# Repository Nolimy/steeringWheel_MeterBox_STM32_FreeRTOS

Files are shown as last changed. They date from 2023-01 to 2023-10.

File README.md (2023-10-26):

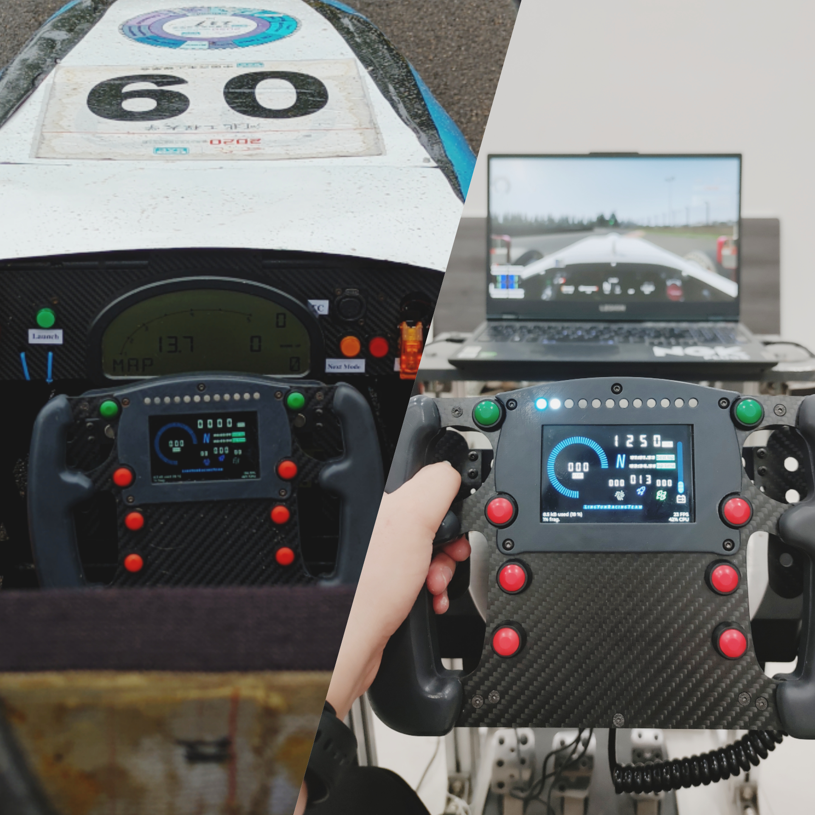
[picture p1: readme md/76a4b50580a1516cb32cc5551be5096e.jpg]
Basic Feature Set


# LY streeringWheel MeterBox

# 关于本项目

本人的本科毕业设计，一款基于STM32F407的大学生方程式赛车方向盘，具体实现功能如下：

1. 采集整车跑动数据（实车模式）以及模拟器数据（模拟器数据），并在仪表上进行实时显示。
2. 通过4G网络，对实车的跑动数据进行实时上传，实现无线数据传输功能。
3. 能够对实车的跑动数据进行采集和保存，方便技术人员对跑动数据进行复盘和分析。
4. 实现控制器功能，能够控制如神力科莎（Assetto Corsa）、神力科莎：争锋（Assetto Corsa Competizione）、F1系列等模拟类赛车游戏。
5. 为了保证实车的可用性，需要具备高亮度的屏幕保证仪表在阳光下的可视效果。
6. 具备可编程按键，实时调整车辆状态。
   
实车使用效果：



模拟器使用效果：

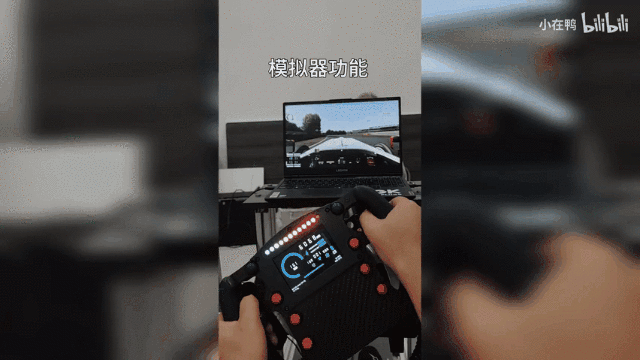
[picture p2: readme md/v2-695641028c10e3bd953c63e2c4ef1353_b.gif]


本项目适用于[大学生方程式赛事](http://www.formulastudent.com.cn/)(👈戳我了解)，因此方向盘外形是依照大学生方程式赛事规则进行设计的。

功能上，实车模式开发基于[河北工程大学凌云车队](https://lingyun.site)(👈戳我了解)凌云Ⅸ号电动方程式赛车。

模拟器功能基于[神力科莎](https://store.steampowered.com/app/244210/Assetto_Corsa/)(👈戳我了解)进行测试。

硬件工程已完整开源在[嘉立创硬件开源平台](https://oshwhub.com/nolimy/steeringWheel_project)(👈戳我了解)，您可以通过该网址访问硬件工程。

项目视频请参考[bilibili](https://www.bilibili.com/video/BV1q24y1T7iM/)(👈戳我了解)

如果项目对您有所帮助，请帮忙点亮一个免费的STAR，开源不易，感谢支持！

---

# 关于开源协议

本项目是开源项目：你可以再分发之和/或依照由自由软件基金会发布的 GNU 通用公共许可证修改之，无论是版本 3 许可证，还是（按你的决定）任何以后版都可以。

发布该项目是希望它能有用，但是并无保障;甚至连可销售和符合某个特定的目的都不保证。请参看 GNU 通用公共许可证，了解详情。

你应该随程序获得一份 GNU 通用公共许可证的复本。如果没有，请看[https://www.gnu.org/licenses/](https://www.gnu.org/licenses/&gt;%E3%80%82)



---

# 关于结构设计

方向盘的外形和结构依照大学生方程式赛事规则进行设计：

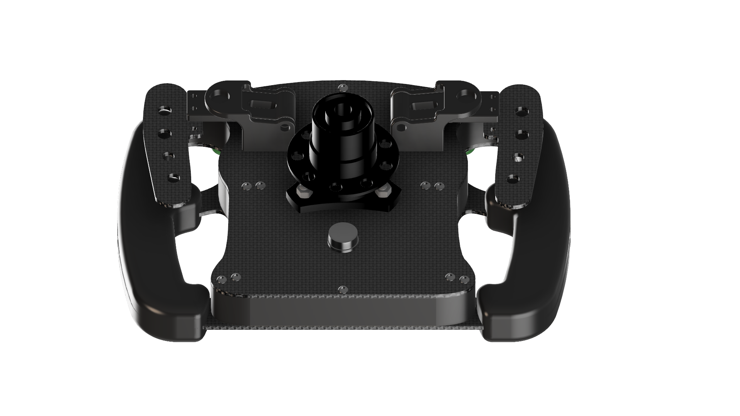
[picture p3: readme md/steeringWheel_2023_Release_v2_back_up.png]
steeringWheel_2023_Release v2_back_up.png


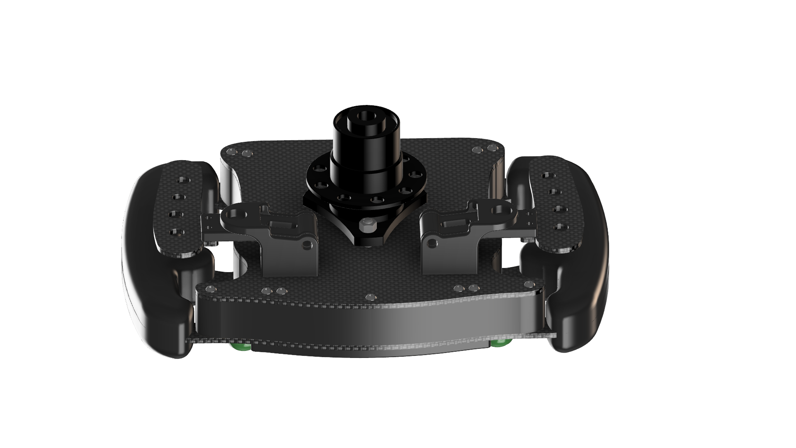
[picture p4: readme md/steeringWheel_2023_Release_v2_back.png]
steeringWheel_2023_Release v2_back.png


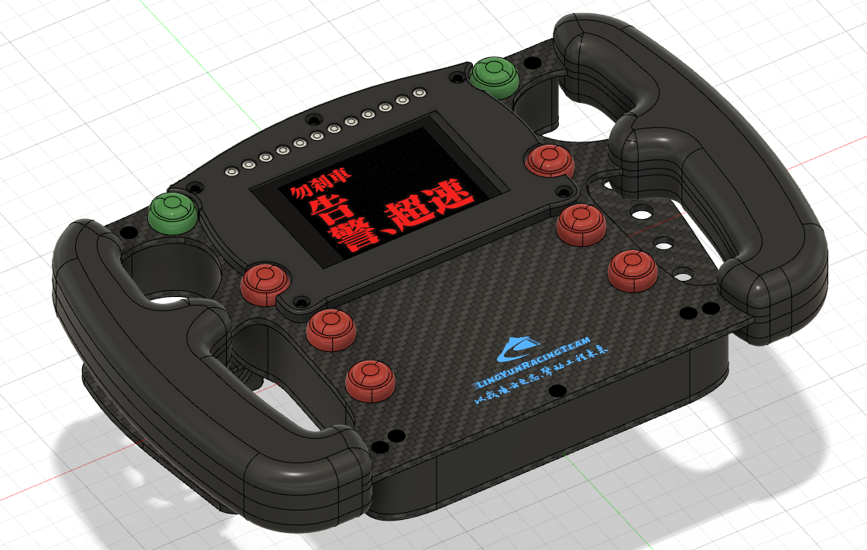
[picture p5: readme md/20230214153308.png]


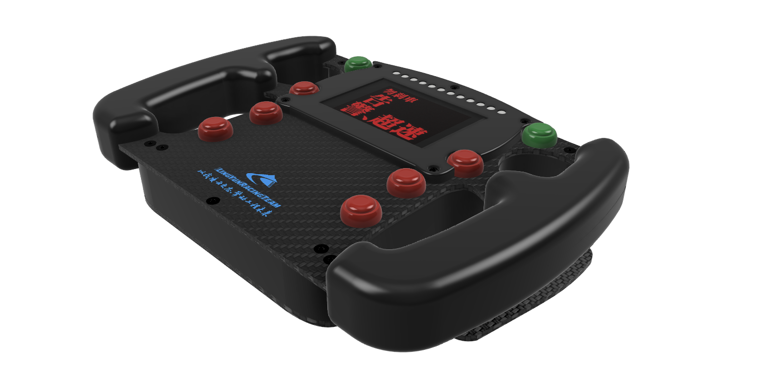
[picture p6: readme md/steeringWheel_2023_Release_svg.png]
steeringWheel_2023_Release svg.png


---

方向盘盘体宽度为250mm，高度170mm。屏幕尺寸为3.5英寸。盘体正面有8个可编程控制器按键。背面安装两个换挡拨片。方向盘上壳体和下壳体使用碳纤维板进行CNC加工，其余零部件如握把、屏幕安装罩、方向盘边缘外壳、换挡拨片连杆及换挡拨片壳体使用黑色树脂进行3D打印加工。

另外设计了一个兼容罗技G27基座的方向盘转接器，所以在我的github仓库中出现了两个3D模型，一个是使用了实车的快拆器（4滚珠），一个是使用了连接到G27的3D打印的方向盘转接器。

BOM配料单请戳👉[我](https://github.com/Nolimy/steeringWheel_MeterBox_STM32_FreeRTOS/blob/main/Steering_Wheel_BOM.xlsx)

[https://github.com/Nolimy/steeringWheel_MeterBox_STM32_FreeRTOS/blob/main/Steering_Wheel_BOM.xlsx](https://github.com/Nolimy/steeringWheel_MeterBox_STM32_FreeRTOS/blob/main/Steering_Wheel_BOM.xlsx)

完整装配模型请戳（实车）👉[我https://github.com/Nolimy/steeringWheel_MeterBox_STM32_FreeRTOS/blob/main/Model/steeringWheel_2023_Release v13.step](https://github.com/Nolimy/steeringWheel_MeterBox_STM32_FreeRTOS/blob/main/Model/steeringWheel_2023_Release%20v13.step)

模拟器：👉[我https://github.com/Nolimy/steeringWheel_MeterBox_STM32_FreeRTOS/blob/main/Model/steeringWheel_2023_Simulator_For_G27 v3.step](https://github.com/Nolimy/steeringWheel_MeterBox_STM32_FreeRTOS/blob/main/Model/steeringWheel_2023_Simulator_For_G27%20v3.step)

3D打印服务推荐嘉立创旗下三维猴：[https://www.sanweihou.com/](https://www.sanweihou.com/), 三维猴提供在线报价，CNC加工，3D打印等一站式服务。

---

# 如何使用

方向盘分为三种模式：待机模式、实车模式和模拟器模式。方向盘上电后，默认为待机模式。当方向盘收到CAN报文，则为实车模式；当方向盘收到串口报文，则为模拟器模式。在待机模式下，电脑可以识别出方向盘为USB设备，但是手柄按键无响应，此时需要使用Simhub的自定义串口设备功能给方向盘发送串口报文，方可进入模拟器模式，模拟器模式手柄按键有响应。因此，使用模拟器模式需要同时使用simhub的自定义串口设备功能。

待机模式下，SLM（换挡LED模块）12颗LED灯珠全部为蓝色。

## 大学生方程式实车使用

方向盘默认使用的是125kbps的波特率，波特率可以使用CubeMX对波特率进行配置和修改，具体CAN协议请根据自家车队的实际情况，修改BSP/CAN中的代码。

## 模拟器使用

### 方向盘连接

模拟器使用需要配合[Simhub](https://www.simhubdash.com/)进行使用。将方向盘使用USB接口连接电脑后，电脑会识别出一个虚拟串口设备和控制器设备：

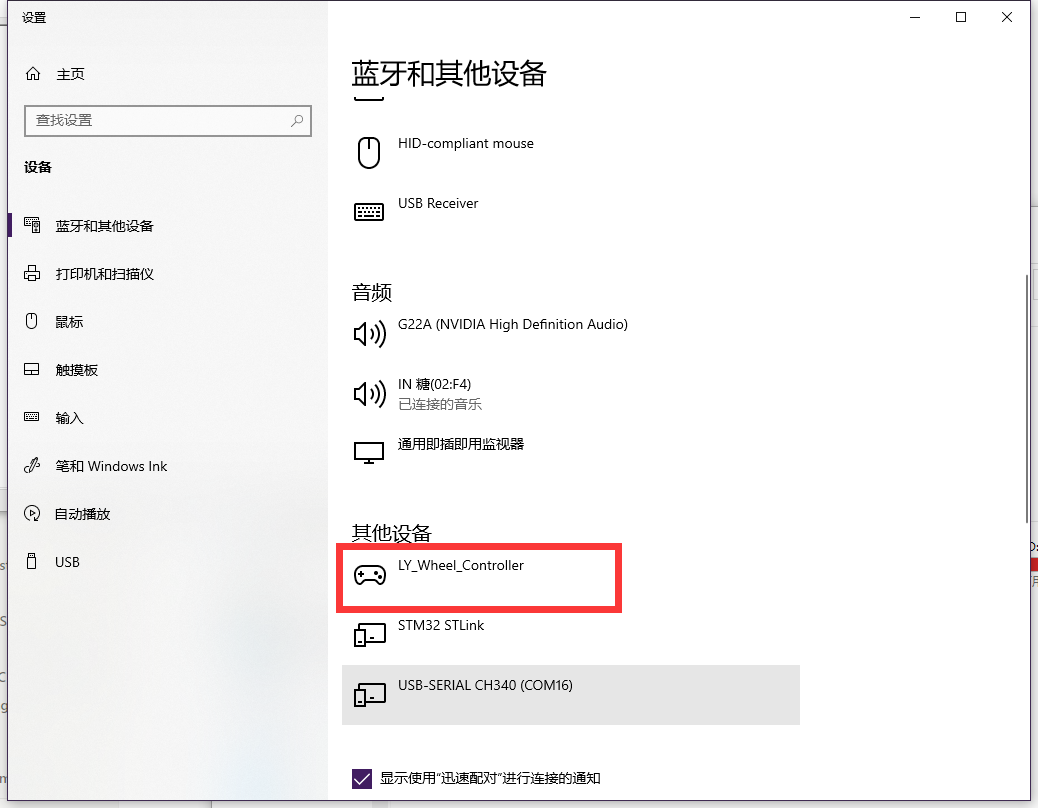
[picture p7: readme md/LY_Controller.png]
在“设置”中的“蓝牙和其他设备”中可以查看到方向盘的LY_Wheel_Controller外设。


在“设置”中的“蓝牙和其他设备”中可以查看到方向盘的LY_Wheel_Controller外设。

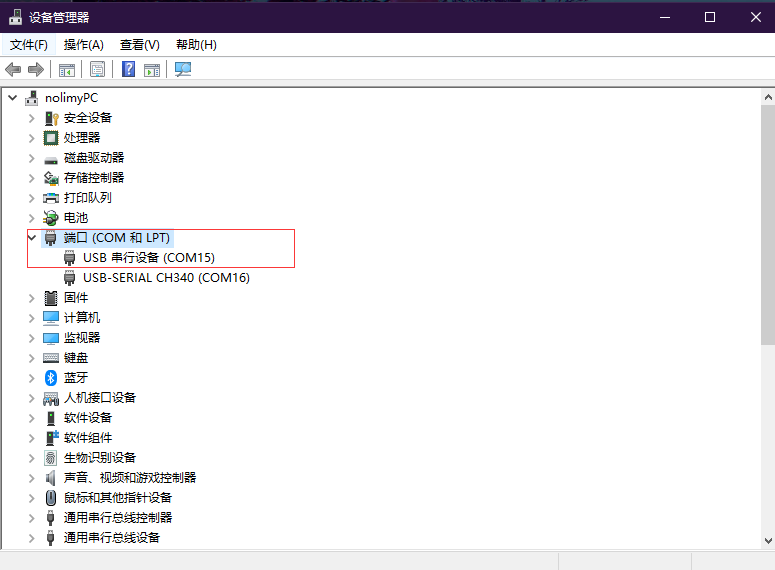
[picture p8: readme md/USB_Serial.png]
在“设备管理器”中可以查看到方向盘的虚拟串口设备及其端口号。


在“设备管理器”中可以查看到方向盘的虚拟串口设备及其端口号。

方向盘控制器的校准，点击“蓝牙和其他设备”右侧的“设备和打印机”:

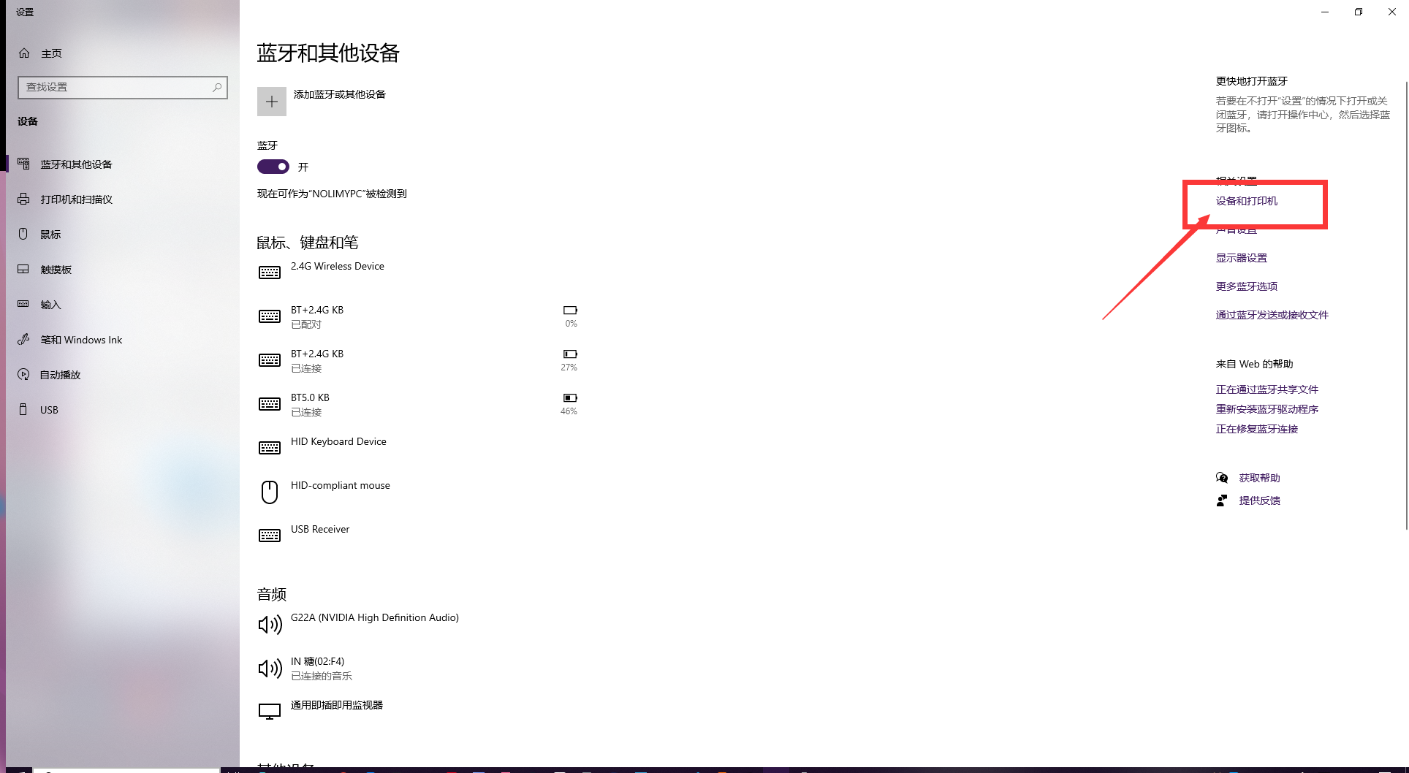
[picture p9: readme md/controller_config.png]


找到”LY_Wheel_Controller”，右键，点击 “游戏控制器设置”，然后点击“属性”.

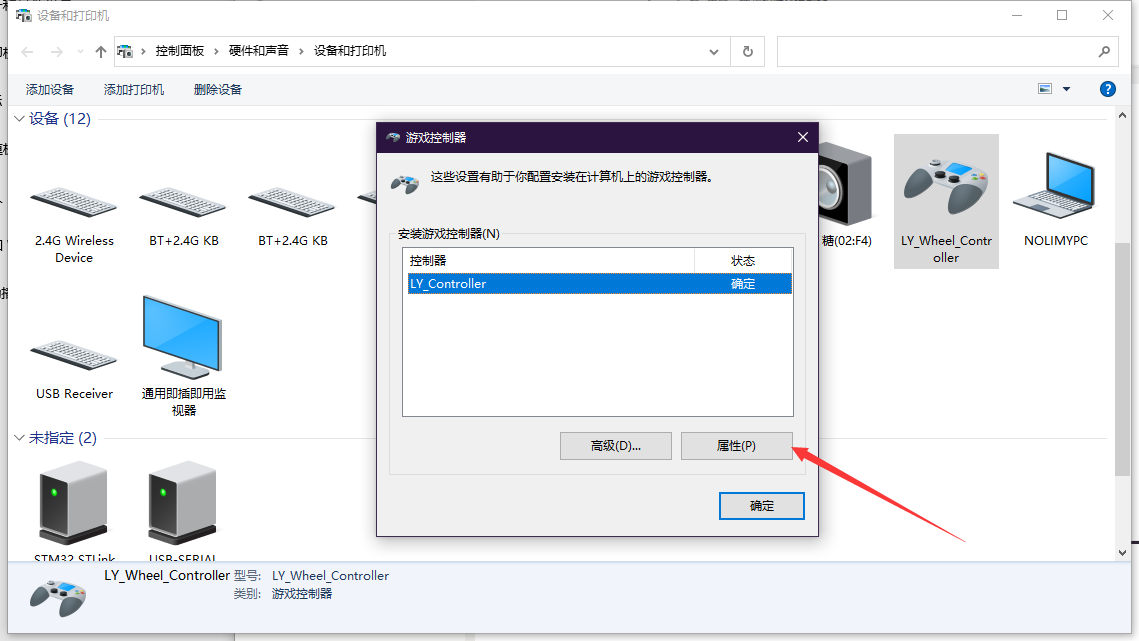
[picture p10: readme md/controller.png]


在测试页中，可以对方向盘的按键进行测试。（默认待机模式下按下方向盘按钮是没有任何反应的）

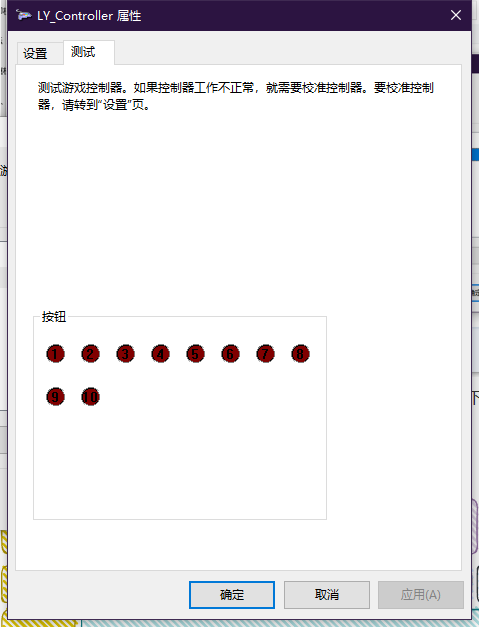
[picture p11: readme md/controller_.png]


### Simhub配置

方向盘的显示功能需要simhub配合使用，可以访问[https://www.simhubdash.com/](https://www.simhubdash.com/)下载simhub软件。这是一个非常强大的软件，支持多种模拟器游戏的数据采集，支持包括汽车仪表、arduino、G力座椅等多种外设。

安装好simhub后，打开设置界面：

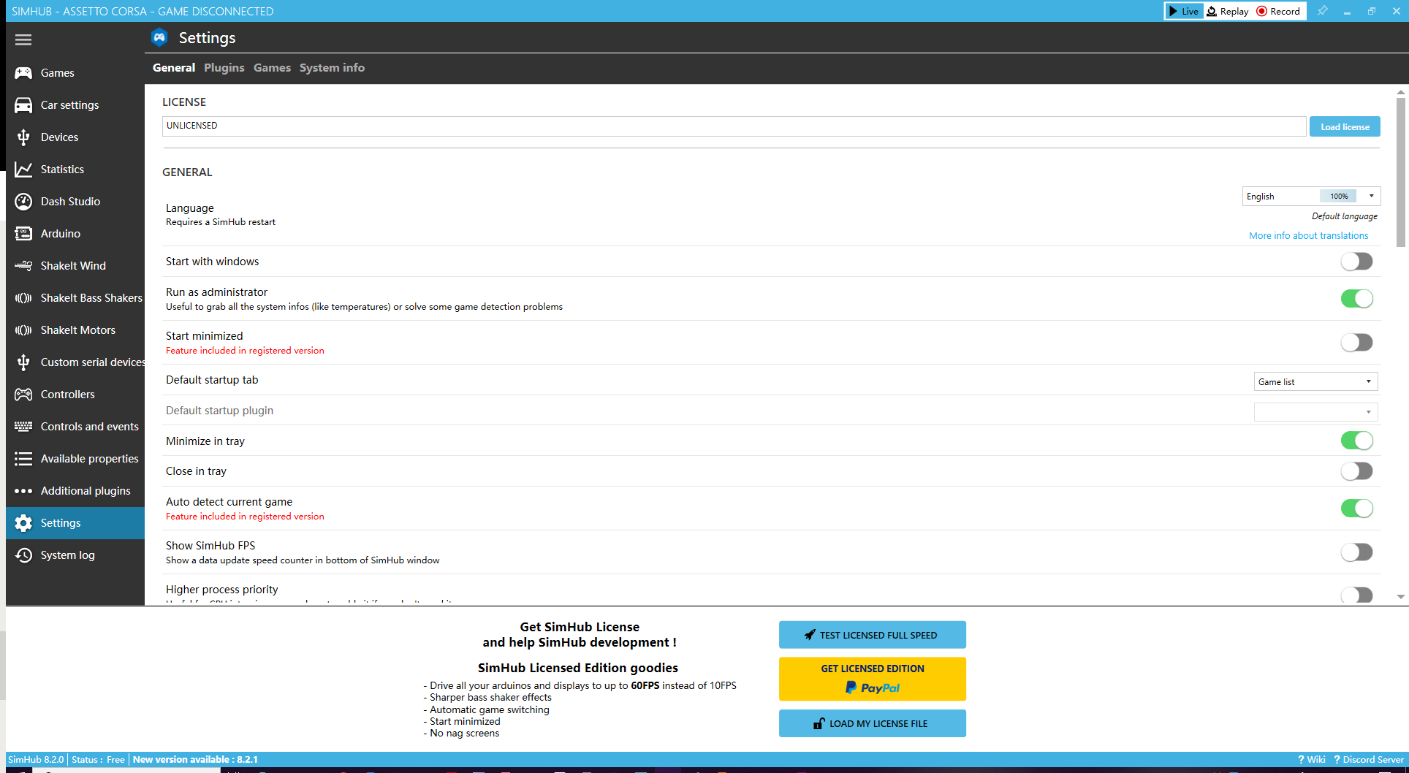
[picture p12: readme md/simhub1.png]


点击插件功能：

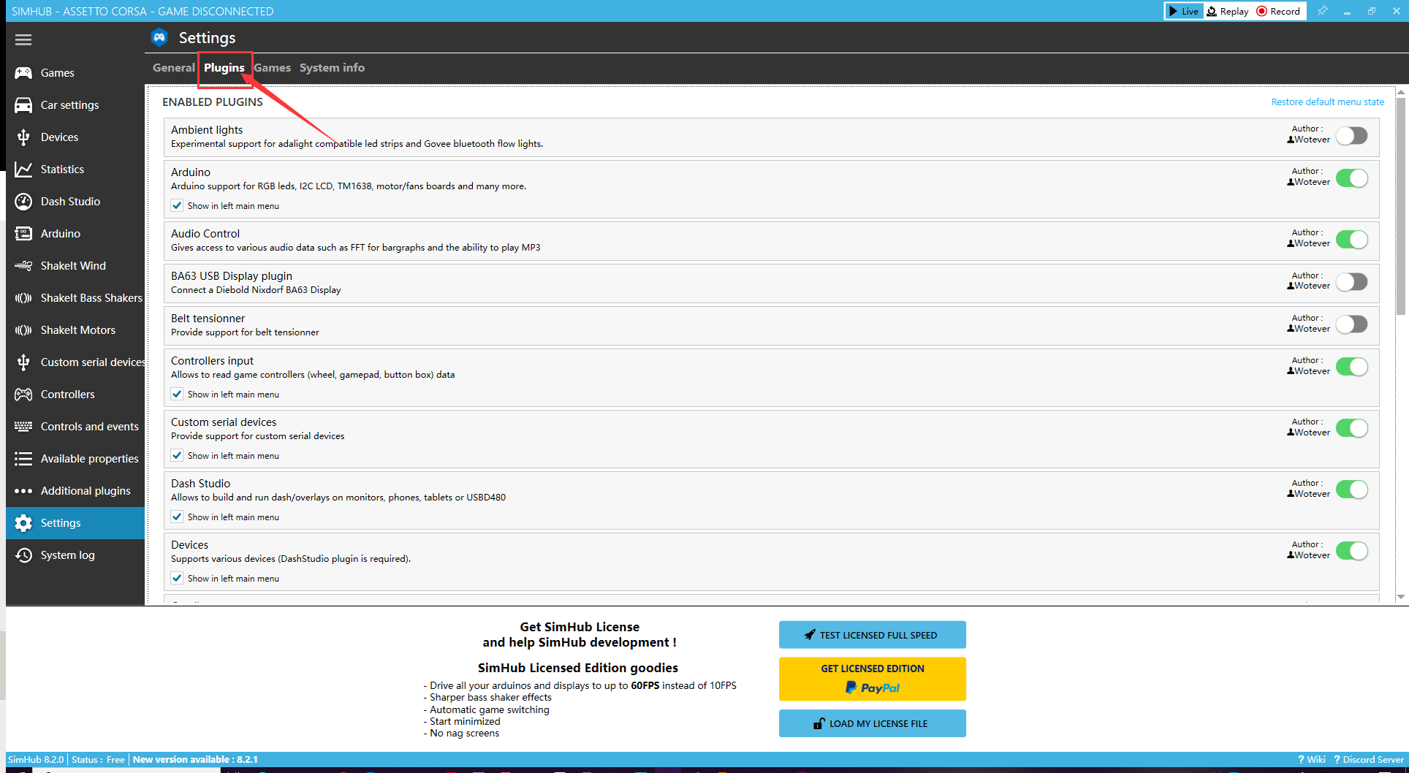
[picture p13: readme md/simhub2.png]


打开”Custom serial devices“插件：

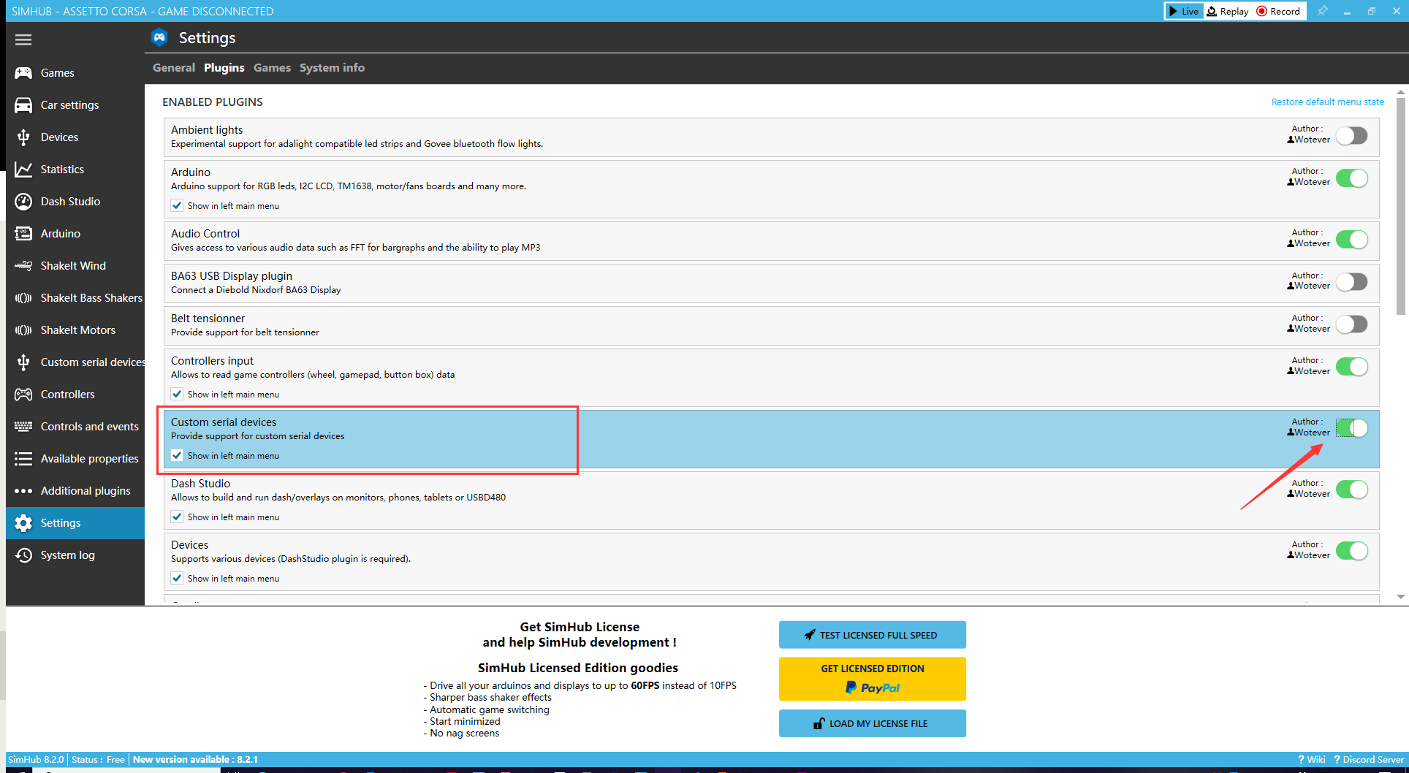
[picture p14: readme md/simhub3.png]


重新打开simhub后，左侧菜单中会出现”Custom Serial Devices”按钮：

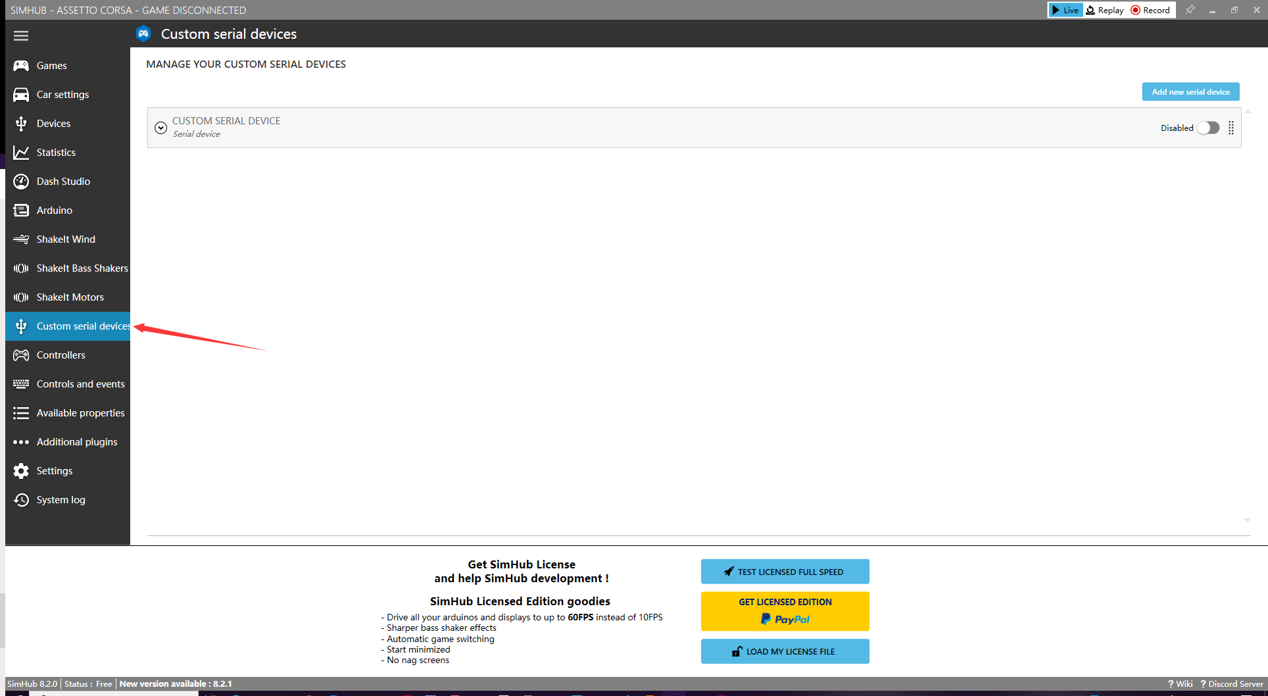
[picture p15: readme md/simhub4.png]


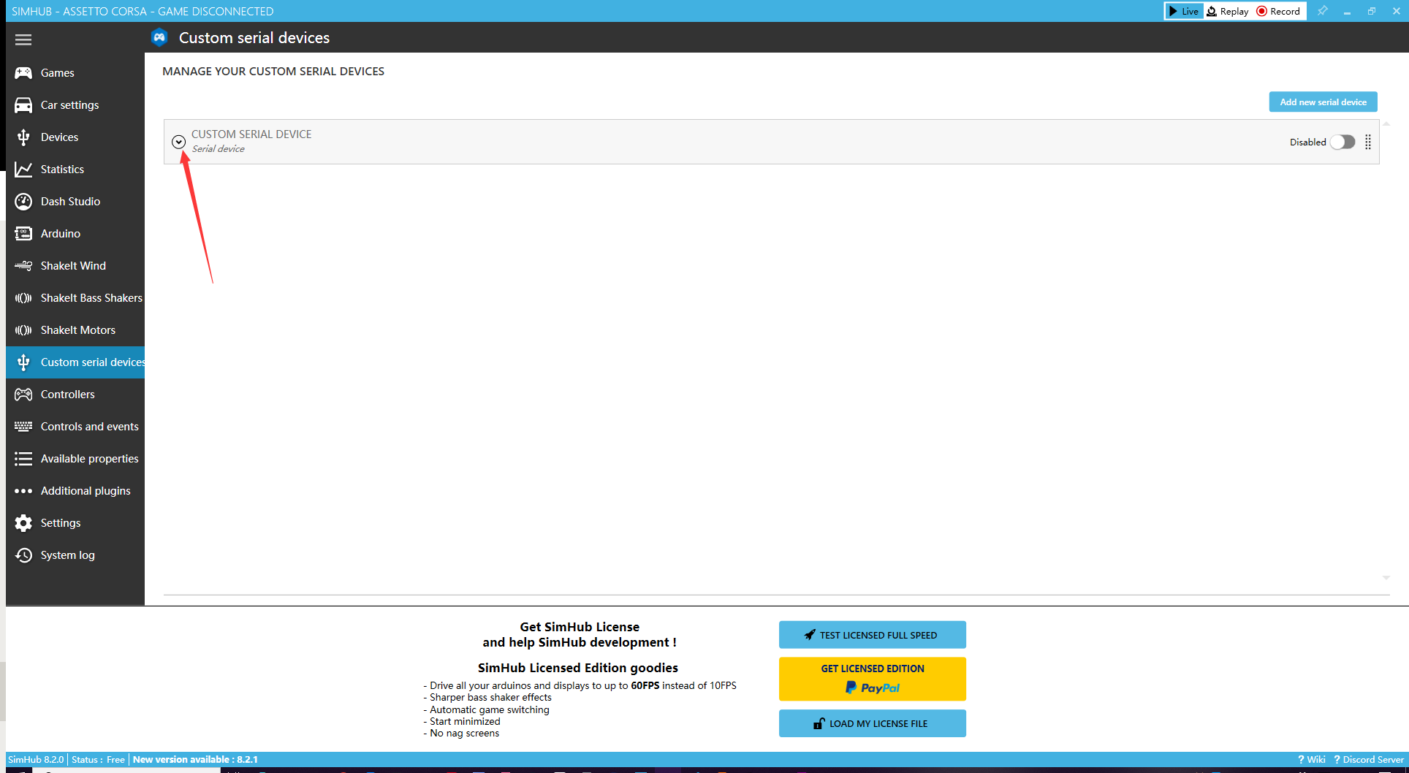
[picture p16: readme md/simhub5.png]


根据设备管理器中显示的方向盘的[串口端口](https://www.notion.so/LY-streeringWheel-MeterBox-ad02f9fb1d354ffdb82a4e431bca5e7d)，选择serial port，我这里使用的是COM15。

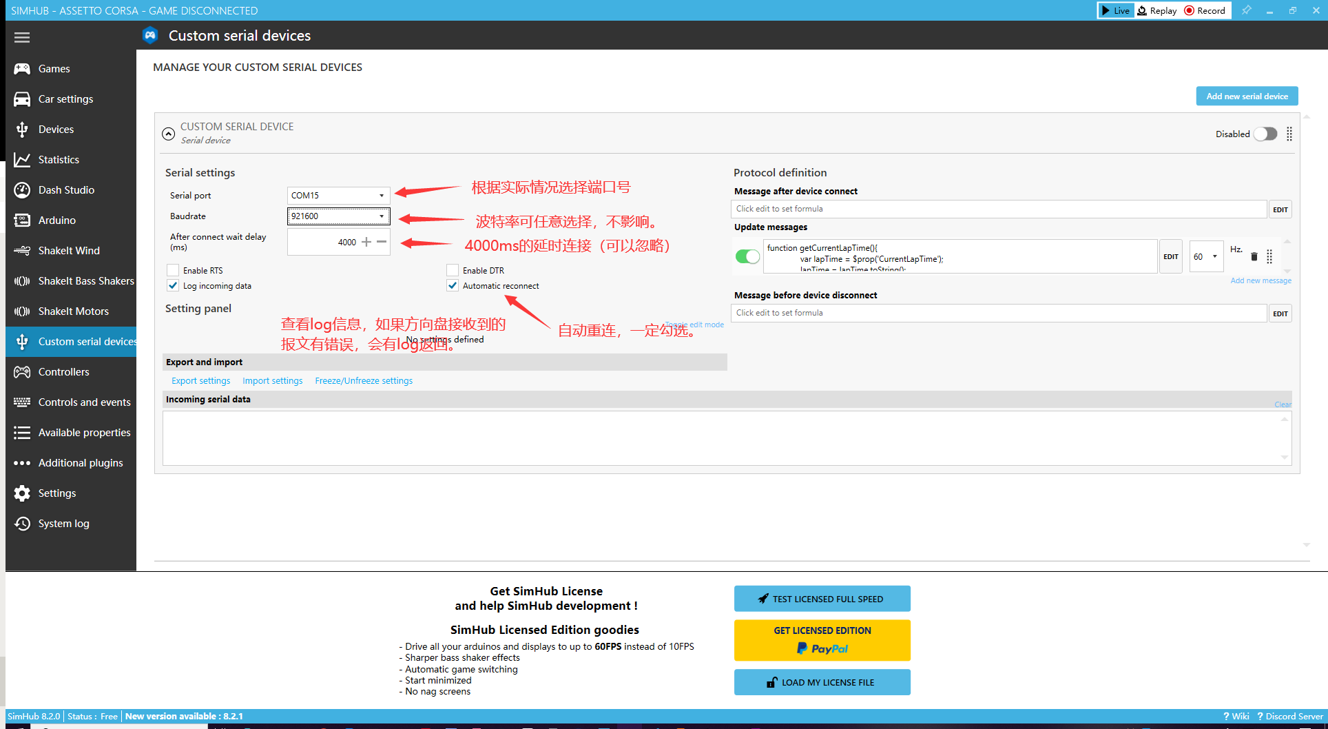
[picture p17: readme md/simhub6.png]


添加游戏数据打包json脚本，将以下javaScript代码粘贴到”Uptate messages“中：

```jsx
function getCurrentLapTime(){
	var lapTime = $prop('CurrentLapTime');
	lapTime = lapTime.toString();
	if(lapTime == "00:00:00")
	{
		return lapTime;
	}
	else
		lapTime = lapTime.toString().slice(3,11);
	return lapTime;
}
function getRPM(){
	var rpm = $prop('DataCorePlugin.GameData.NewData.Rpms');
	rpm = format(rpm,"0");
	return rpm;
}
function getSpeed(){
	var speed = $prop('SpeedKmh');
	speed = format(speed, '0');
	return speed;
}
function getGear(){
	var gear = $prop('Gear');
	return gear;
}
function getBestLapTime(){
	var bestLapTime = $prop('BestLapTime');
	bestLapTime = bestLapTime.toString();
	if(bestLapTime == "00:00:00")
	{
		return bestLapTime;
	}
	else
		bestLapTime = bestLapTime.toString().slice(3,11);
	return bestLapTime;
}
function getFuel(){
	var fuel = $prop('FuelPercent');
	fuel = format(fuel, '0');
	return fuel;
}
function getRedLine(){
	var redLine = $prop('CarSettings_CurrentGearRedLineRPM');
	return redLine;
}
function getBrake(){
	var brake = $prop('Brake');
	brake = format(brake, '0');
	return brake;
}
function getThrottle(){
	var throttle = $prop('Throttle');
	throttle = format(throttle, '0');
	return throttle;
}
function getLap()
{
	lap = $prop('CurrentLap');
	return lap;
}
var speed = getSpeed();
var carData = "{\"speed\":" + getSpeed() + ",\"rpm\":" + getRPM() + ",\"cLapTime\":" +"\"" + getCurrentLapTime() + "\"," +"\"gear\":" + "\"" +getGear() + "\"" + ",\"bLapTime\":" +"\"" + getBestLapTime() + "\""+ ",\"fuel\":"+ getFuel() + ",\"redLineRPM\":"+ getRedLine()
  + ",\"brake\":" + getBrake() + ",\"throttle\":"+ getThrottle()  + ",\"lap\":"+ getLap() +"}";
return carData;
```

点击”Edit”:

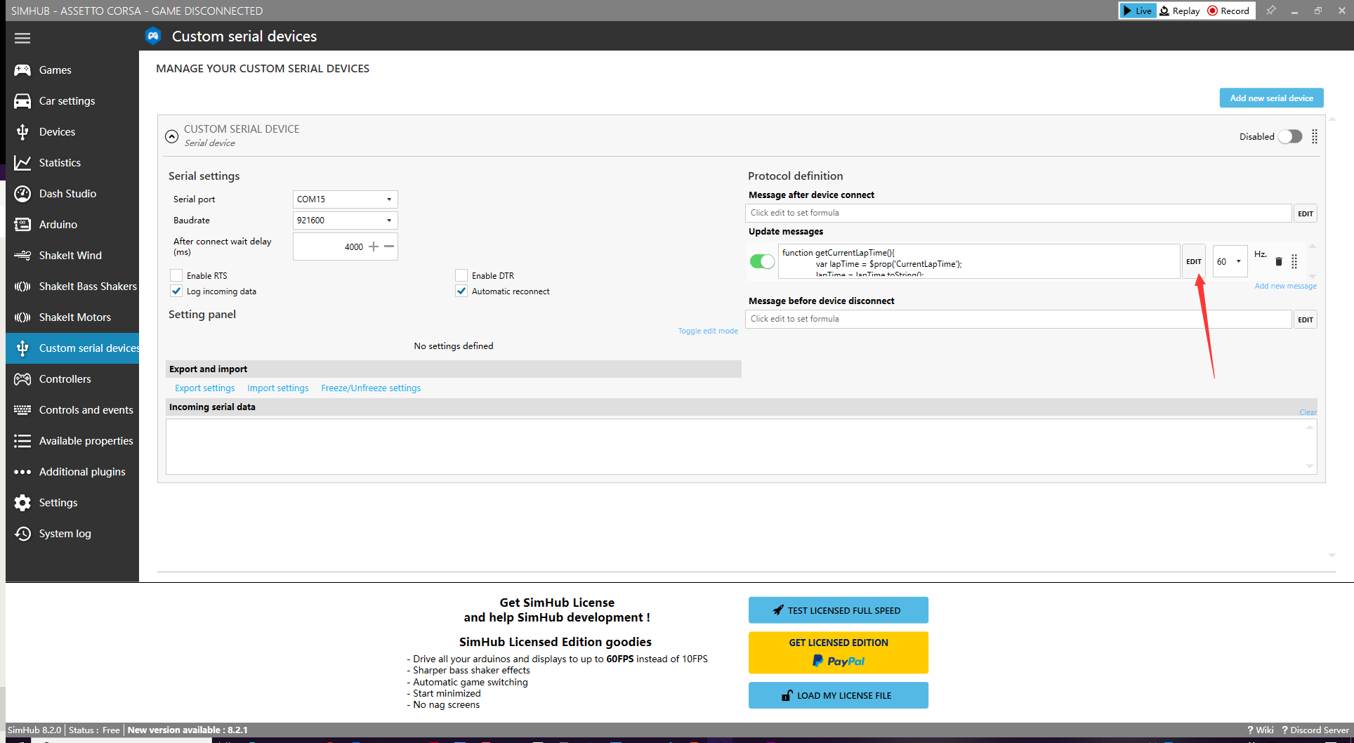
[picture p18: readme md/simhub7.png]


点击”Computed value“：

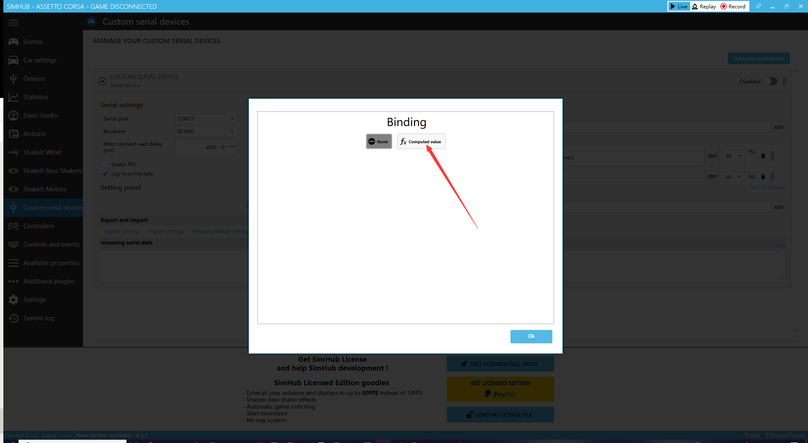
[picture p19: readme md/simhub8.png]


勾选”Use JavaScript”:

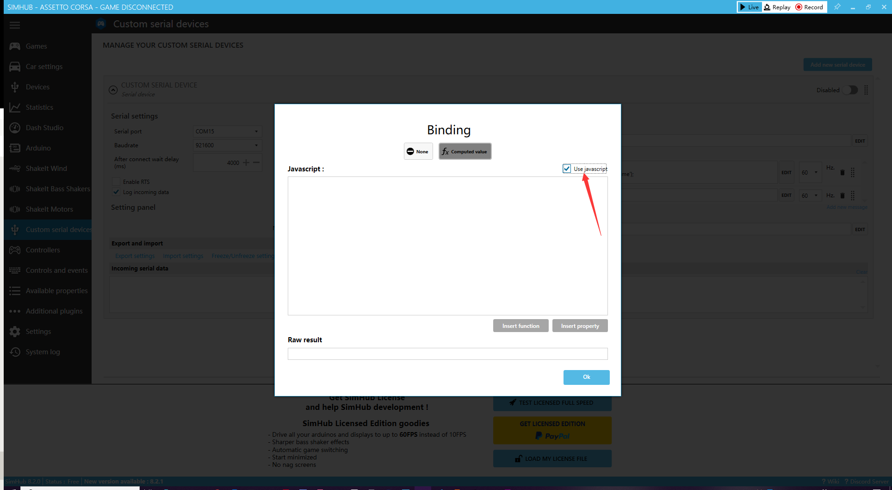
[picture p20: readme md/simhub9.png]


将[代码](https://www.notion.so/LY-streeringWheel-MeterBox-ad02f9fb1d354ffdb82a4e431bca5e7d)粘贴到文本框中：

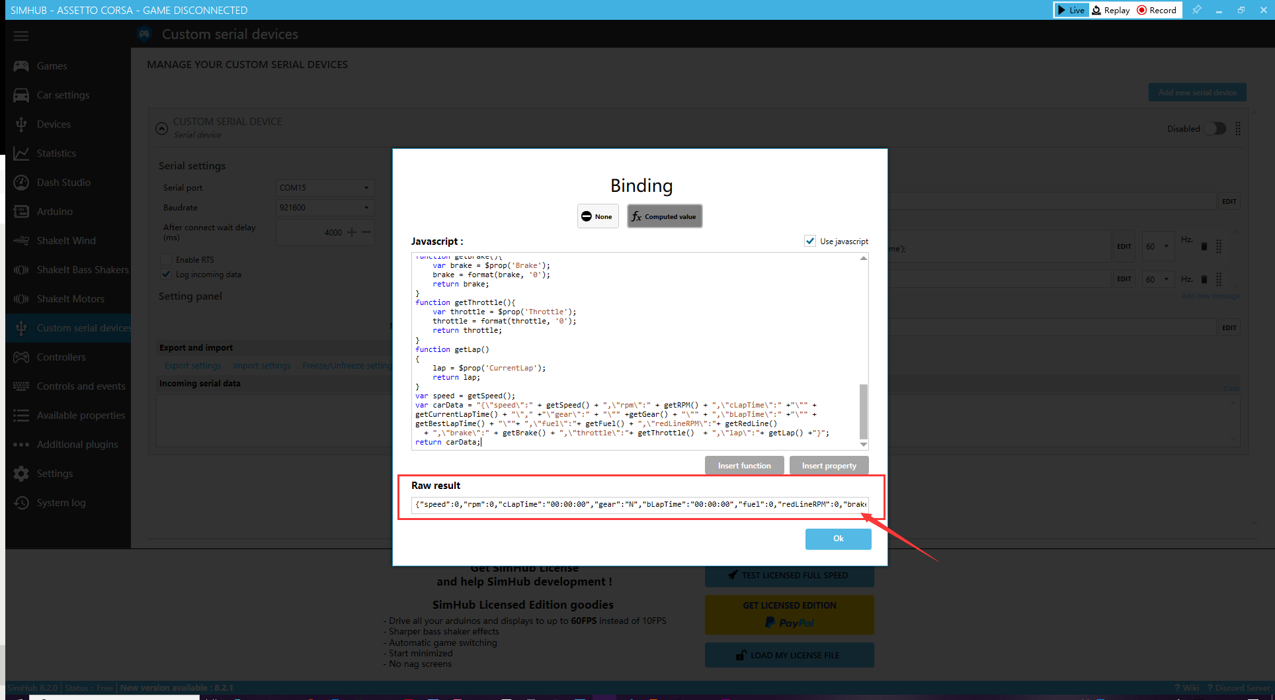
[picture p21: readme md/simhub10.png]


正常情况下Raw result中可以生成完整的json字符串。最后点击连接按钮，稍等片刻，就可以看到方向盘的SLM的全部蓝灯熄灭，此时进入模拟器模式。这时进行[手柄按键测试](https://www.notion.so/LY-streeringWheel-MeterBox-ad02f9fb1d354ffdb82a4e431bca5e7d)，可以看到按钮可以被正常检测到。



### 游戏内配置

以”Assetto Corsa“为例，在保证simhub后台运行的条件下，启动游戏。进入控制设置，将模拟器键位改成识别到的控制器按键键位，如下图：

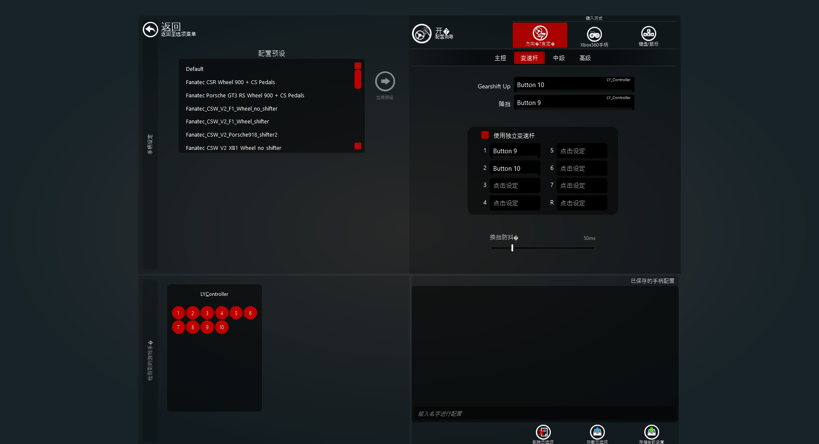
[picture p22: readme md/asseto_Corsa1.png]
asseto Corsa1.png


接下来启动游戏，就可以拥有和实车方向盘一样的体验了。

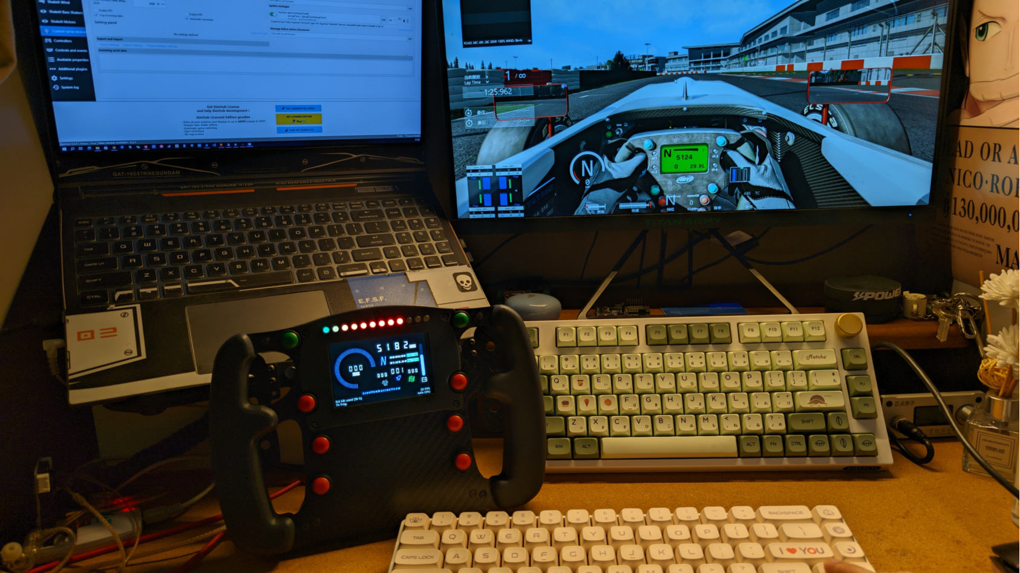
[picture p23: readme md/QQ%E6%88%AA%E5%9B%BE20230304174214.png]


# 目 录

[第1章 绪论](#绪论)

[1.1 课题研究的背景及意义](#11-课题研究的背景及意义)

[1.2 方向盘工作原理概述](#12-方向盘工作原理概述)

[1.2.1 方向盘机械结构](#121-方向盘机械结构)

[1.2.2 实车功能方案](#122-实车功能方案)

[1.2.3 模拟器功能方案](#123-模拟器功能方案)

[第2章 系统总体设计方案](#系统总体设计方案)

[2.1 硬件设计方案](#_Toc137138264)

[2.1.1 系统功能需求分析](#211-系统功能需求分析)

[2.1.2 硬件选型](#212-硬件选型)

[2.2 软件设计方案](#_Toc137138267)

[2.2.1 方向盘软件架构设计](#221-方向盘软件架构设计)

[2.2.2 MQTT服务器架构](#222-mqtt服务器架构)

[第3章 硬件开发设计及方案验证](#硬件开发设计及方案验证)

[3.1 STM32主控引脚资源分配](#31-stm32主控引脚资源分配)

[3.2 主机原理图设计](#32-主机原理图设计)

[3.2.1 STM32最小系统电路](#321-stm32最小系统电路)

[3.2.2 LCD屏幕驱动电路](#322-lcd屏幕驱动电路)

[3.2.3 BC260Y模块外围电路设计](#323-bc260y模块外围电路设计)

[3.2.4 CAN通信接口设计](#324-can通信接口设计)

[3.2.5 SLM LED电路](#325-slm-led电路)

[3.2.6 TYPE-C USB电路](#326-type-c-usb电路)

[3.2.6 其他接口电路](#326-其他接口电路)

[3.3 PCB Layout设计](#33-pcb-layout设计)

[第4章 STM32最小系统基础驱动配置](#stm32最小系统基础驱动配置)

[4.1 时钟配置](#41-时钟配置)

[4.2 STM32 SYS配置](#42-stm32-sys配置)

[4.3 数据交互层代码设计](#43-数据交互层代码设计)

[第5章 GUI仪表界面开发](#gui仪表界面开发)

[5.1 HAL层配置](#51-hal层配置)

[5.2 BSP层开发](#52-bsp层开发)

[5.3 APP层——LVGL开发](#53-app层lvgl开发)

[5.3.1 LVGL移植](#531-lvgl移植)

[5.3.2 LVGL界面设计](#532-lvgl界面设计)

[第6章 实车数据采集功能开发](#实车数据采集功能开发)

[6.1 CAN通信HAL层配置](#61-can通信hal层配置)

[6.2 CAN通信BSP层配置](#62-can通信bsp层配置)

[6.3 CAN APP层代码开发](#63-can-app层代码开发)

[第7章 模拟器相关功能实现](#模拟器相关功能实现)

[7.1 模拟器功能HAL层开发](#71-模拟器功能hal层开发)

[7.2 模拟器功能BSP层开发](#72-模拟器功能bsp层开发)

[7.3 模拟器相关功能APP层](#73-模拟器相关功能app层)

[第8章 无线数传功能开发](#无线数传功能开发)

[8.1 HAL层开发](#81-hal层开发)

[8.2 BC260Y BSP层开发](#82-bc260y-bsp层开发)

[8.3 BC260Y APP层开发](#83-bc260y-app层开发)

[8.4 无线数传测试](#84-无线数传测试)

[第9章 SLM功能模块开发](#slm功能模块开发)

[9.1 SLM HAL层开发](#91-slm-hal层开发)

[9.2 SLM BSP层驱动开发](#92-slm-bsp层驱动开发)

[9.3 SLM APP层开发](#93-slm-app层开发)

[第10章 总体功能整合](#总体功能整合)

[10.1 系统功能启动逻辑设计](#101-系统功能启动逻辑设计)

[10.2 FreeRTOS 进程配置](#102-freertos-进程配置)

[第11章 总结](#总结)

[11.1 方向盘机械结构设计](#111-方向盘机械结构设计)

[11.2 功能测试](#112-功能测试)

[11.3 待改进之处](#113-待改进之处)

[参考文献](#参考文献)

[致 谢](#致-谢)

# 绪论

## 1.1 课题研究的背景及意义

中国大学生方程式系列赛事（Formular Student China）（简称“FSC”）是一项由高等院校汽车工程或汽车相关专业在校学生组队参加的汽车设计与制造比赛。各参赛车队按照赛事规则和赛车制造标准，在一年的时间内自行设计和制造出一辆在加速、制动、操控性等方面具有优异表现的小型单人座休闲赛车，能够成功完成全部或部分赛事环节的比赛。中国大学生方程式系列赛事包括四个分赛项：中国大学生方程式汽车大赛（燃油车）、中国大学生电动方程式大赛、中国汽车工程学会巴哈大赛以及中国大学生无人驾驶方程式赛事。[1]迄今为止，我国参加FSC赛事的参赛队伍已经有超过100多支，该赛事为我国汽车工业输送了大批优秀人才，是汽车工程师的摇篮。

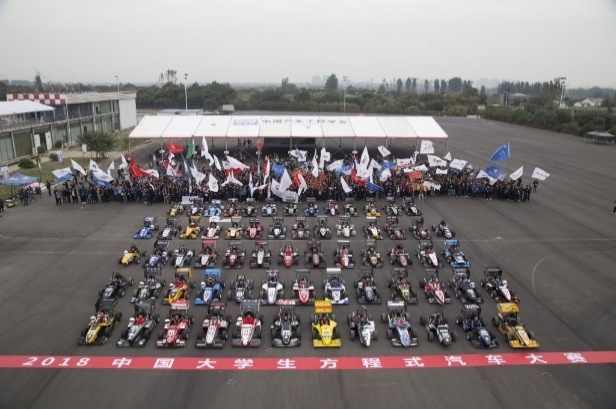
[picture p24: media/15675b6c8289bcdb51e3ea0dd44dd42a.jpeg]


中国大学生燃油方程式赛车是指使用以汽油作为动力的单座小型休闲赛车。参赛车队根据赛事规则设计并制造赛车，并进行一系列的动态跑动测试，包括直线加速、八字环绕、高速避障和耐久测试。如图1-2为河北工程大学凌云车队2020赛季参赛油车——凌云Ⅷ号赛车。该赛车搭载凯旋675发动机，使用MoTeC M800作为ECU对发动机进行自主标定和控制。该赛车使用了机械增压装置、电动离合、气动换挡、无线数传系统等设计。

中国大学生电动方程式赛车是使用电力作为动力来源的方程式赛车，如图1-3为凌云车队在2022赛季参赛的凌云Ⅸ号电动方程式赛车，该赛车使用两个EMRAX208高压轮边电机作为动力总成，使用自行设计的额定电压为444V的高压电池作为动力来源，峰值功率为150kW，最大转速为6000RPM，设计最高车速为120km/h。

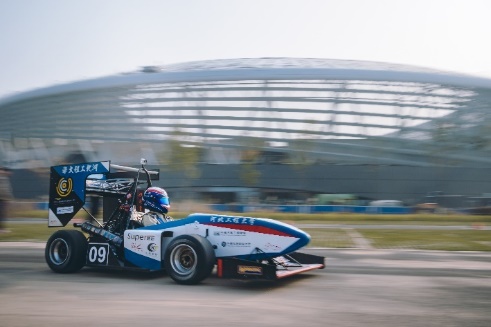
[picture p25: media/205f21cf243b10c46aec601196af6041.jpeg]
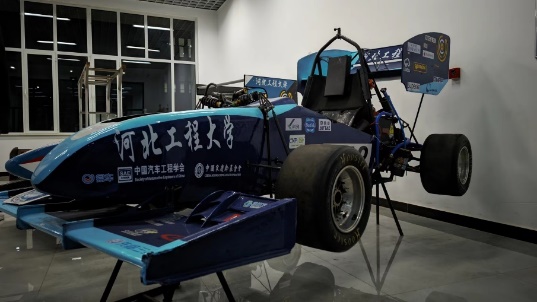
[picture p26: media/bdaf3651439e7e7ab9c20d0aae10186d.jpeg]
|  图12 凌云Ⅷ号燃油方程式赛车 |  图13 凌云Ⅸ号电动方程式赛车 |
|---|---|

在大学生方程式赛事中，各家车队使用的数据采集系统主要分为两种，一种是使用与MoTeC ECU相配套的MoTeC官方赛用仪表，如CDL3、C125等，这类仪表功能强大，具备有数据采集、数据显示、数据分析等功能，但价格普遍偏贵，市场价在2\~3万元人民币不等；另外一种是使用车队自制的仪表系统，这类仪表大都是使用普通的如LCD1602液晶显示器作为屏幕，显示效果差，但成本很低，开发难度不高。如图1-4为MoTeC的CDL3仪表，图1-5为北京理工大学使用的自制仪表屏幕面板。

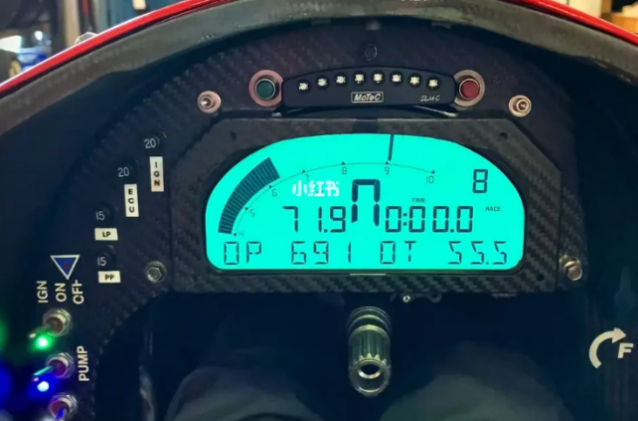
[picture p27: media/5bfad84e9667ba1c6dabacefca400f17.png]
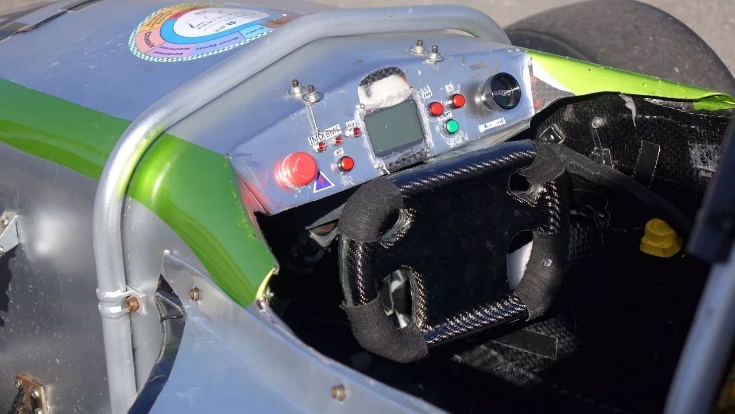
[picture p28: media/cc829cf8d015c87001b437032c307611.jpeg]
|  图14 MoTeC CDL3仪表 |  图15 北京理工大学自制仪表面板 |
|---|---|

而在更高级别的方程式赛事中，例如F1、F2方程式赛事等，这些赛车的数据采集系统是集成在方向盘上的，绝大多数赛车的方向盘作为一个独立的终端被集成在赛车中，对车辆的跑动数据进行采集，同时方向盘上的按钮可以实时控制车辆功能，例如改变当前的跑动策略，甚至与维修区的工程师进行实时通信，这就要求方向盘不但具备有基础的控制车辆转向的功能，同时可以作为一个数据采集的终端，收发车辆的数据。在为车手反馈车辆跑动状态的同时，还能够将采集到的数据实时打包发送给P房的策略师和工程师，对车辆的状态进行实时监控。如图1-6为法拉利F1车队的方向盘盘面。

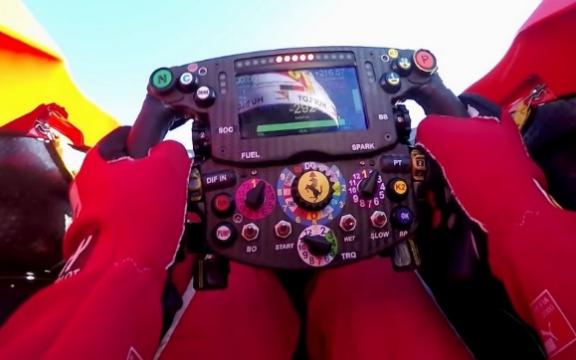
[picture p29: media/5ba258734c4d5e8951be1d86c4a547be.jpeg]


图16 法拉利F1方程式赛车方向盘

国外一些大学生方程式车队已经采用了类似上述F1方程式赛车的方向盘设计方案，将数据采集系统集成在方向盘内部，以达到更高的集成度。如下图为波兰的Wroclaw University of Technology大学生方程式赛车队PWR Racing Team的RTⅩ赛车设计并制造的使用集成数据采集系统和仪表显示的方向盘，该系统采用了自行设计的硬件系统，通过接入到赛车的整车CAN网络，对行车电脑的数据进行解算后将数据显示到屏幕。

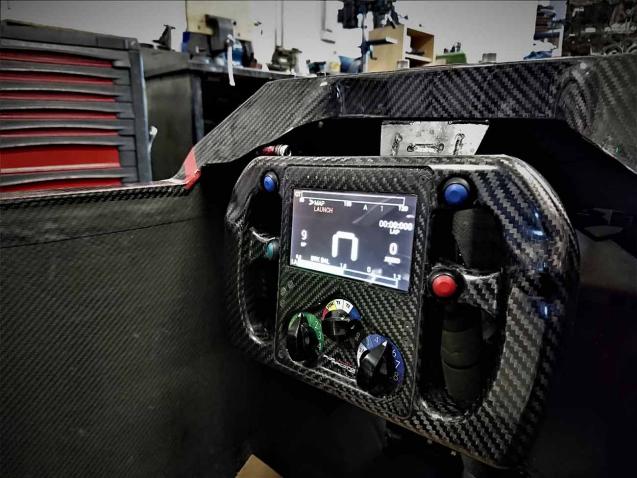
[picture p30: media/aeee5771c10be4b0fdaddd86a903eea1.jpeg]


图17 PWR RTⅩ' s Steering Wheel

动态项目作为大学生方程式系列赛事中不可或缺的比赛方式，其对车手的驾驶技能要求很高。因此，车手的日常训练就显得尤为重要。由于实车训练会导致资源消耗，如轮胎磨损、燃油消耗、场地限制等，同时具有一定危险性，因此实车训练虽然重要但是成本比较高，实际在日常练车中频率较低，车手训练更多采用的方式是使用驾驶模拟器进行训练。模拟器技术是由汽车的线控底盘技术演变而来，具备有换挡拨杆、手刹器、踏板、伺服电机转向基座等装置，基于计算机模拟技术，通过将专用的控制器接入到计算机，与相应的模拟软件配合，即可达到模拟实车驾驶跑动的目的。如下图1-8为F1方程式车手训练时使用的模拟器设备。对于大学生方程式赛事，更多车队使用的模拟器设备如图1-9所示，相较于F1等高级别方程式车手训练所使用的设备来说略显简陋，但是能达到拟真实车跑动驾驶体验的目的，对车手驾驶技能的训练有显著的提升作用。

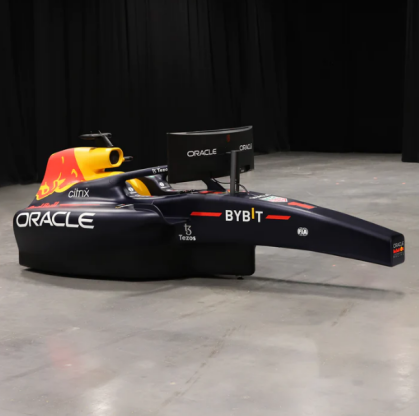
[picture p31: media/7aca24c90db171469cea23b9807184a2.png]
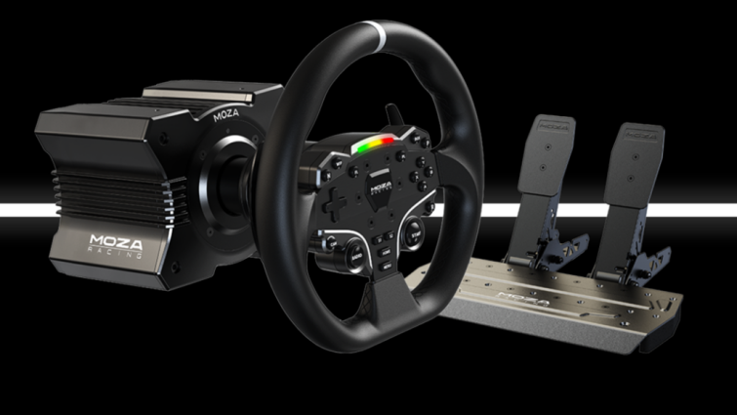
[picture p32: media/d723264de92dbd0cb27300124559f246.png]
|  图18 红牛F1车队模拟器装置 |  图19 国内市场上某品牌直驱模拟器产品 |
|---|---|

模拟器软件方面，国内大学生方程式车队中被广泛使用的模拟软件是由意大利游戏开发商Kunos Simulazioni开发的《神力科莎》（意大利语：Assetto Corsa, 英语：“Racing Setup”），如图1-10为该软件的画面。这款游戏的定义是“赛车模拟器”，通过激光扫描赛道与细致的物理引擎还原各种公路车型和赛道车型提供逼真的驾驶体验。游戏支持一系列外设，包括键鼠、游戏手柄、方向盘模拟器装置。为保证逼真的拟真体验，车手训练时会使用方向盘模拟设备使用该软件。一个很有特色的功能在于，游戏中的HUD可以通过扩展外设的方式扩展到计算机以外的其他硬件，如模拟器方向盘的屏幕上能够显示当前模拟器软件中车辆跑动的实车状态，相当于形成了一个真实的仪表。如图1-11为模拟器方向盘的仪表显示模拟器的车辆跑动数据。

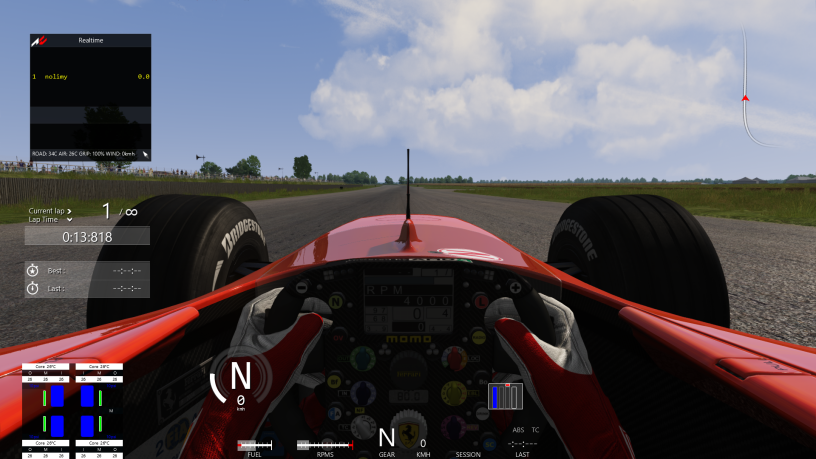
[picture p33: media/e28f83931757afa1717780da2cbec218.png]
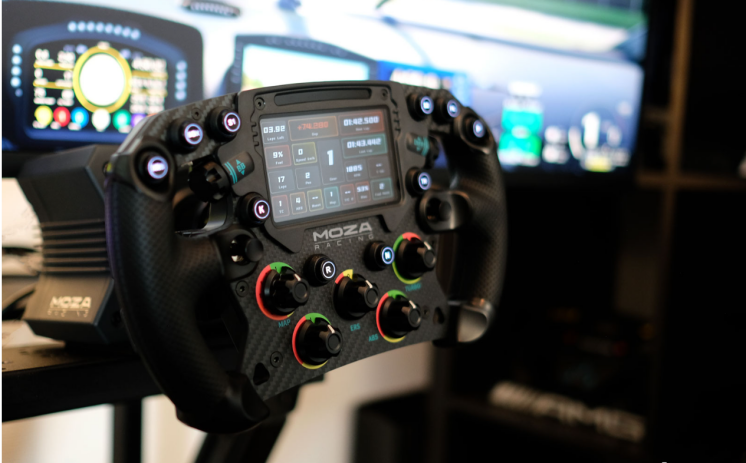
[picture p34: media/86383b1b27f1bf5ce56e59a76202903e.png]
|  图110 神力科莎模拟F1方程式赛车跑动 |  图111 方向盘显示模拟器跑动数据 |
|---|---|

综上，在大学生方程式系列赛事中，实车上使用的仪表和数据采集系统可以借鉴更高级别方程式赛车的设计思路，将其整体集成在方向盘内部，使方向盘不再仅仅是一个用于转向的工具。而模拟器上常见的带有仪表显示功能的方向盘，其外形和功能上与实车的方向盘基本一致，因此可以考虑将方向盘设计成实车和模拟器相互兼容的设备，在大学生方程式的车手日常训练时，使用同一块方向盘进行实车和模拟器的训练，对实车和模拟器的数据分别进行采集和显示。

基于上述几种当前赛场上常见的数据采集系统，本项目旨在设计一款低成本、兼容性强、功能强大、集成在方向盘中的仪表系统，具备有数据采集、仪表显示、无线数据传输等功能。同时兼容大学生方程式实车和模拟器设备。具体功能描述如下：

（1）采集大学生方程式系列赛事赛车的实车跑动数据（实车模式）以及模拟器数据（模拟器模式），并在仪表上进行实时显示。

（2）通过4G网络，对实车的跑动数据进行实时上传，实现无线数据传输功能，工程人员可以通过上位机查看赛车的实时跑动状态。

（3）实现控制器功能，能够对如神力科莎、神力科莎：争锋、F1系列模拟类赛车游戏。

（4）为保证实车在阳光下的仪表可视条件，需要具备高亮度仪表保证良好的显示效果。

（5）具备可编程按键，能够对实车功能进行控制，如进行车辆的换挡、ABS调节等功能。

（6）具备换挡提示灯条，即根据当前发动机转速提示车手进行升档降档操作的灯条。英文称之为Shift LED Module(SLM)。

## 1.2 方向盘工作原理概述

### 1.2.1 方向盘机械结构

机械结构设计主要依据《中国大学生方程式大赛规则-2022》中对转向结构及方向盘形状的规则进行设计。规则中要求：“方向盘轮廓必须为连续闭合的近圆形或近椭圆形。例如：方向盘的外轮廓可以有一些部分趋向直线，但不可以有内凹的部分。禁止使用 H 形、8 型或外轮廓有开口的方向盘。”同时规则中还要求方向盘在任何转角下的最高点都不能高于方程式赛车前环的最高点，这是对车手手部安全的保护。但由于驾驶舱内空间狭小，若是方向盘太大、太低，可能会和车手的大腿发生干涉；如果方向盘太小又可能导致车手在转向时更加费力。所以需要在多个条件限制下找到最适合的方向盘尺寸和定位设计方案。参考其他级别方程式赛车的盘面设计，采用带圆角的长方形。如下图1-12为河北工程大学凌云车队在2019赛季使用的方向盘轮廓设计。

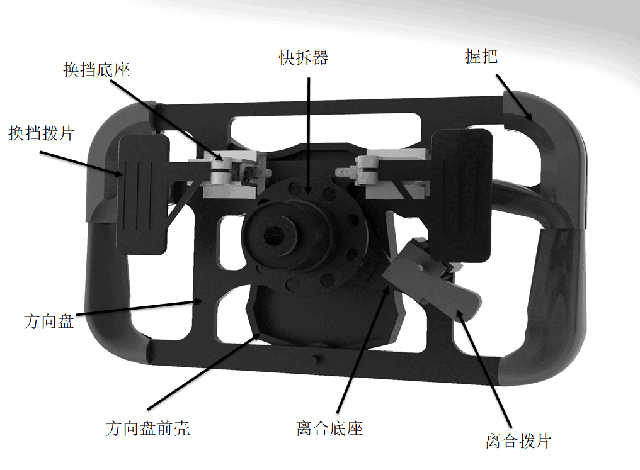
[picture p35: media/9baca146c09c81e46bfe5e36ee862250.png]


图112 凌云车队2019赛季方向盘

在制作工艺上可以选择复合材料或是3D打印来进一步轻量化。在车手握方向盘的地方可以添加手模，或是缠绕增加摩擦力的纱布，便于车手握紧方向盘。参考美国艾克朗大学ZIPS Racing方程式赛车队2019\~2020赛季的设计报告[2]，方向盘可以采用三明治结构进行设计，使用3D打印技术和CNC技术进行制造，其中，握把使用FDM 3D[3,4]打印技术进行制造，方向盘使用碳纤维板进行CNC切割。方向盘必须由坐在驾驶座上的人快速卸下，无需使用工具，因此需要通过在转向柱末端处焊接一个快速释放花键来完成，这个花键与安装在方向盘背面的一个快拆器配合使用。快拆器可以选型购买市面上常见的方程式赛车快拆器，只需在方向盘主体上依照快拆器安装螺栓位置预留好安装孔位即可。为了保证轻量化设计，方向盘主体可以进行镂空，为了保证镂空后的方向盘强度，需要对镂空后的方向盘模型进行有限元受力分析，保证方向盘轻量化设计的同时具备足够的强度。

### 1.2.2 实车功能方案

实车功能上主要分为数据采集、数据显示、车辆控制、无线数传功能四部分。其中数据采集是所有功能的基础。数据采集方面，方向盘通过CAN接口接入到整车CAN网络，通过接收并解析整车控制器或ECU在CAN网络中广播出来的特定CAN报文，即可获取到实车跑动数据，如车速、电机或发动机转速、节气门开度、踏板开度等。将采集到的CAN报文解析成物理数值后，主控芯片将相关数据渲染到仪表界面，实现数据显示功能[5.6]。车辆控制功能通过在方向盘盘面预留出按键，主控芯片通过GPIO读取按键状态，将控制信号转为CAN信号发送到CAN网络，整车控制器或者其他CAN网络中的控制单元接收相应的CAN报文进行相应功能的响应。无线数传基于4G模块，将采集的车辆跑动数据打包好通过MQTT协议发送到云端服务器实现无线数传功能。

### 1.2.3 模拟器功能方案

模拟器功能相对实车功能比较简单，通过USB将方向盘连接到电脑，方向盘作为复合USB设备，电脑将方向盘识别成两个USB设备，分别是虚拟串口和joystick控制器设备。通过Simhub软件将模拟赛车软件中的跑动数据打包成json报文从虚拟串口发送给方向盘，方向盘将解析后的跑动数据渲染到仪表界面。控制器功能基于joystick USB设备，通过编写USB的设备描述符，将方向盘的按钮开关信号采集后通过USB发送给电脑，即可实现模拟器的控制器功能。

# 系统总体设计方案

## 2.1 硬件设计方案

依据预期设计目标，该方向盘主要接收和发送CAN报文以及USB虚拟串口报文，因此需要基础的CAN收发电路和USB TypeC接口；同时使用4G模块上传数据，需要设计单独的4G模块电路；保存跑动数据到FLASH，所以需要外部FLASH的外围电路；仪表显示则需要基础的屏幕驱动电路；同时需要对实车和模拟器进行基础的控制，故需要按键电路；其他的还包括基于WS2812B LED的全彩换挡提示模块（Shift LED Module,，简称SLM），以及主控芯片基础的外围电路如晶振电路和供电电路等[7]。

如图2-1为系统总体框图。

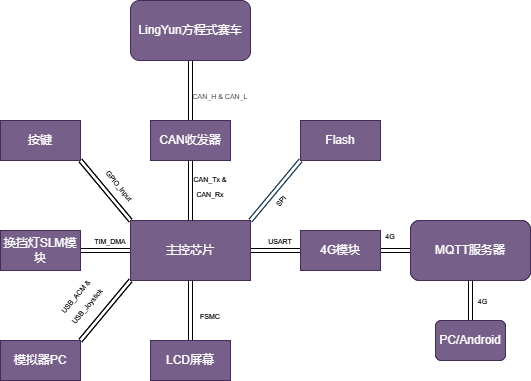
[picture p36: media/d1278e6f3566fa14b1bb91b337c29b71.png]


图21 系统总体框图

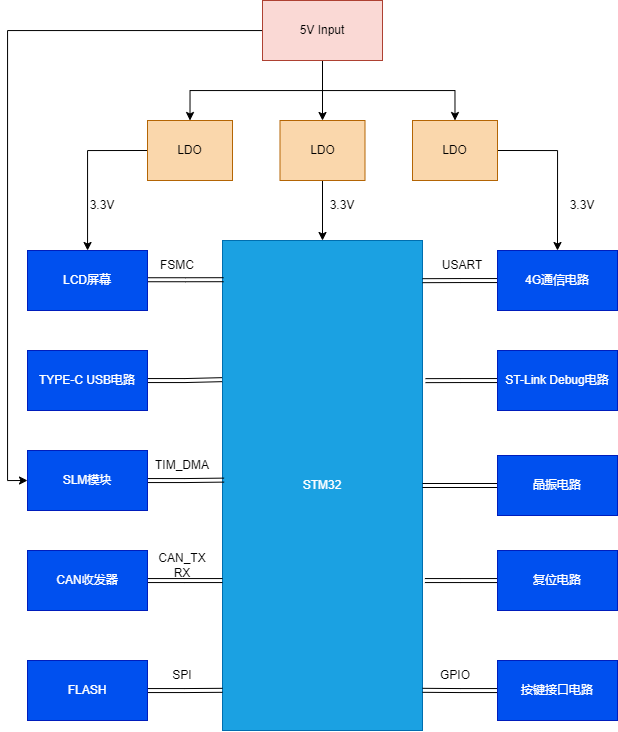
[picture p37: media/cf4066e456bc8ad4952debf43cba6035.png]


图22 硬件系统框图

### 2.1.1 系统功能需求分析

需要实现方向盘在接收到实车或者模拟器电脑发送的CAN数据或串口数据后，能够将解析好的物理数值如车速、发动机转速等渲染到屏幕上，同时在实车模式下将采集好的车辆跑动数据通过4G模块发送到云端方便其他人员查看实时跑动状态，并将数据保存到外部FLASH。方向盘具备控制功能，需要通过采集按键信号，发送相应的控制指令给车辆和模拟器。另外有独立的SLM模块能够依据当前发动机转速提示车手进行升档降档操作。

### 2.1.2 硬件选型

主控的选型，根据以上分析方向盘所涉及到的功能，我们需要主控同时具备有如下外设接口：给LCD屏幕使用的FSMC接口、与4G模块通信的至少1路的USART接口、与外部FLASH通信的SPI接口、至少1路CAN控制接口、至少3路可编程定时器、足够的GPIO接口、支持全速USB功能接口。同时为了保证仪表的显示效果，主控需要处理大量的图形界面相关的运算，因此需要至少128KB的RAM，同时为保存图片字体等图形资源，FLASH也需要足够大。主控的主频直接决定了仪表的运行效果，因此选型的主控需要有足够高的运行频率。如图2-3为本项目所使用到的所有外设接口图。

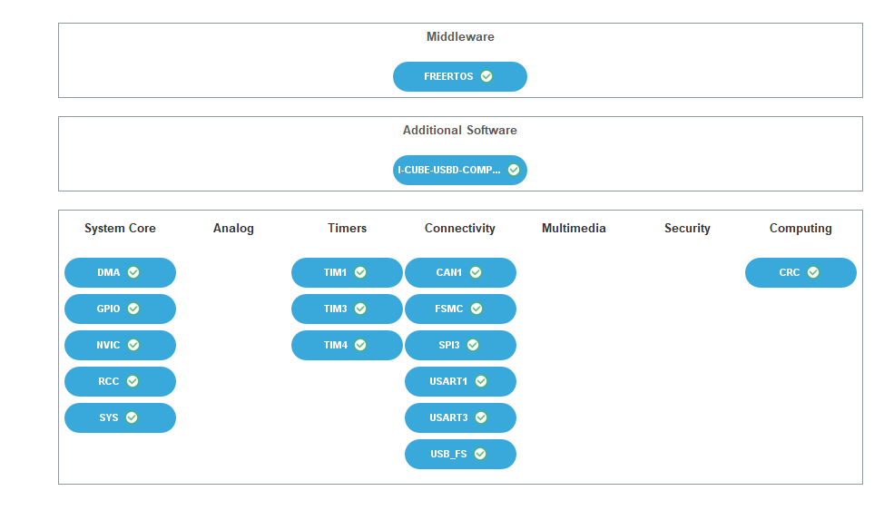
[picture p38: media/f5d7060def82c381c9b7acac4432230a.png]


图23 方向盘外设接口框图

除了主控需要具备有相应的外设资源和优异的性能以保证功能的实现，还要考虑到经济性，尽量选择价格低、货量充足的芯片作为我们的主控。最终我们选择了STM32F4系列的STM32F407ZET6，其具备有192KB RAM，512KB 片上FLASH，以及168MHz的时钟运行频率，该芯片为LQFP144封装，具备有足够本项目使用的GPIO外设接口，同时该封装便于手工焊接和贴片焊接。如图2-4为STM32F407ZET6芯片。

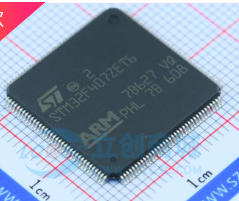
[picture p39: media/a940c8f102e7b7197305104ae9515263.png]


图24 STM32F407ZET6

4G模块上，我们选择上海移远通信的BC260Y模块，该模块支持多种网络协议：UDP/TCP/MQTT，同时具备有AT命令功能的串口，方便与主控进行通信。同时该模块能够接入到阿里云等物联网云平台，具有很强的可扩展性。

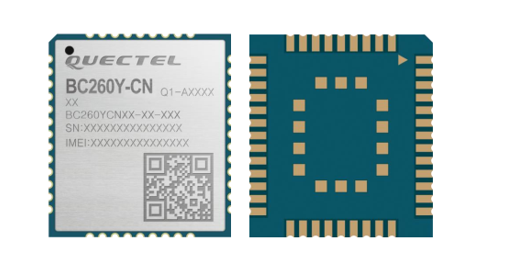
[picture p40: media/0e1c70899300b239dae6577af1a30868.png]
|  图25 BC260Y-CN |  图26 BC260Y引脚分配图 |
|---|---|

LCD屏幕选型方面，基于方向盘尺寸的考虑，我们选择使用3.5inch的屏幕。为了保证仪表在阳光直射条件下依然有良好的可视效果，市面上常见的屏幕很难满足高亮度可视需求，因此我联系到了屏幕供应商柯达科，他们提供了一款亮度可以达到1000尼特的LCD屏幕。其屏幕型号为KD035HVFMD145-01，通信协议支持SPI及8080协议。其主要参数如表2-1所示：



图27 该屏幕在阳光下的显示效果

表21 KD035HVFMD145-01

| 主控 | 材质 | 亮度 | 色彩 | 分辨率 | 尺寸 | 供电电压 |
|---|---|---|---|---|---|---|
| ST7796 | TFT  | 950cd/m2 | 65K/262K | 480\*320 | 3.5inch | 3.3V |

CAN收发器的选型上，经过综合价格、性能、供货速度等因素考量[8,9]，我采用了TJA1050芯片作为方向盘的CAN收发器。TJA1050的主要特征如下：

（1）完全符合ISO 11898标准。

（2）最高速率可达到1Mbit/s，完全符合大学生方程式赛车的CAN网络的波特率要求。

（3）电磁辐射极低，同时具备有很强的电磁抗干扰性能。

（4）保护总线引脚，防止汽车环境中的瞬态干扰。

（5）STM32的CAN控制接口为3.3V电压，赛车CAN网络为5V，TJA1050具备输入级和3.3V以及5V 的器件兼容能力。

（6）防止电池对地的短路。

SLM模块和仪表屏幕一样需要满足在阳光下可视的要求，因此选型使用WS2812B作为SLM模块的显示元件，其峰值亮度可达到1200尼特。这款LED使用PWM进行控制，仅需一个控制引脚即可实现多个LED的串联控制，具体特点如下：

（1）IC控制电路与LED点光源共用一个电源。

（2）控制电路与RGB芯片集成在一个5050封装的元器件中，构成一个完整的外控像素点。

（3）内置信号整形电路，任何一个像素点收到信号后经过波形整形后输出，保证线路波形畸变不会累加。

（4）内置上电复位和掉电复位电路。

（5）每个像素点的三基色可实现256级的亮度显示。完成16777216种颜色的全真色彩显示。

（6）端口扫描频率为2KHz/s。

（7）串行级联接口，能通过一根信号线完成数据的接收与解码。

（8）数据发送速度可达800Kbps.





图28 WS2812B典型应用电路



图29 WS2812B实物

外部FLASH选用华邦的W25Q128芯片，其具有16Mbytes的容量，可以存储大约1\~2h的实车跑动数据。该芯片使用SPI与STM32主控进行通信，同时其封装可以与华邦其他同系列的不同容量芯片相同，在保证外部电路和封装不变的情况下更换其他容量FLASH芯片十分便捷。



图210 W25Q128JVSIQ

综上所述，具体的硬件架构如下图所示：



图211 详细的硬件架构图

## 2.2 软件设计方案

软件上主要分为基于方向盘硬件的固件、无线数传所使用的MQTT服务配置以及相应的无线数传上位机开发。

### 2.2.1 方向盘软件架构设计

基于方向盘的硬件设计以及要实现的功能，我们的软件架构选择垂直结构，考虑到方向盘要实现的功能比较复杂，且实时性要求较高，因此在软件上使用到了嵌入式实时操作系统FreeRTOS，通过实时操作系统的任务进程管理，将需要同时运行的功能任务分成多个进程，分时运行。如下图2-11为系统整体架构：



图212 系统整体架构

软件层主要分为HAL（硬件抽象层）、Database（数据层）、BSP层（板级支持包）、

APP层（应用层）、操作系统。

HAL层代码通过ST意法半导体公司官方的MCU图形化配置工具生成，通过图形化界面配置好项目中使用到的外设，如串口、SPI、CAN等外设，即可生成相应的驱动代码。以串口为例，我们可以在图形界面中使能串口功能，并配置硬件控制流、中断、DMA，以及基本的波特率、字长、停止位等设置。配置完成后通过GENERATE CODE按钮即可生成相应的C代码。



图213 CubeMX串口配置页面

Database层中定义了上层应用中所使用到的所有变量和常量定义，其作用是为了避免变量的重复定义与.h头文件的重复引用和声明，使代码结构清晰，同时便于变量内存的管理，增强代码的可维护性和可读性。

BSP层是根据HAL层提供的硬件接口代码编写的，是沟通HAL层和APP层的桥梁，其作用是将APP层和HAL层分隔开，避免APP层直接调用HAL层代码，增强代码的可移植性。根据功能需求，BSP层有以下模块构成：

（1）BSP_W25Q128：对应硬件上的外部FLASH W25Q128芯片，主要调用HAL层的SPI相关代码，实现FLASH的读写操作，为APP层的FATFS提供相应的接口代码。

（2）BSP_BC260Y：对应硬件上的4G模块 BC260Y模组，主要调用HAL层的USART相关代码，实现BC260Y初始化、连接网络、错误回调等功能，为APP层的MQTT应用提供接口代码。

（3）BSP_CAN：对应硬件上的CAN收发器TJA1050，主要调用HAL层的CAN相关代码，实现CAN接收中断、CAN滤波器初始化等功能，为APP层的LY_CAN报文解析协议应用提供接口代码。

（4）BSP_USB：对应硬件上的USB接口，硬件上使用TYPEC接口连接计算机。主要调用HAL层的USB相关代码，实现USB的复合设备功能，如ACM虚拟串口接收中断、JoyStick的按键等功能，为APP层的Simhub应用提供接口代码。

（5）BSP_LCD：对应硬件上的LCD显示屏，主要调用HAL层的FSMC相关代码，基于8080协议，与LCD主控进行通信，进行基本的读写操作，提供有相应的屏幕亮屏、初始化、画点、画线等功能，为APP层的LVGL图形库提供接口代码。

（6）BSP_WS2812B：对应硬件上的WS2812B LED模块，主要调用HAL层的TIM向相关代码，基于定时器DMA输出可变的PWM波形，控制WS2812B模块的显示颜色，提供有基本的点灯函数和WS2812B的颜色控制函数，为APP层的SLM功能提供基础的接口代码。

（7）Usart_Printf：对应主控上的三路Usart，主要调用HAL层的USART相关代码，定义了printf重定向函数，方便进行项目调试，为所有APP层的模块提供printf输出接口，便于Debug。

APP层为应用代码层，定义了所有功能的具体实现的逻辑代码。为FreeRTOS系统提供接口函数。FreeRTOS的进程代码中直接调用APP层封装好的函数，如MQTT打包上传函数，SLM转速响应函数等。

FreeRTOS对APP层定义的所有功能进行统筹规划，通过FreeRTOS的进程管理，保证方向盘所有功能稳定运行。

综上所述，具体的软件架构图如下图所示：



图214 软件架构图

### 2.2.2 MQTT服务器架构

基于选用的4G模块BC260Y所支持的TCP/UDP/MQTT网络协议，综合稳定性、可维护性和成本上的考虑，选择使用MQTT（Message Queuing Telemetry Transport）协议作为无线数传的传输协议。MQTT协议是基于TCP/IP协议上为硬件性能低下的远程设备设计的基于客户端-服务器的消息发布/订阅传输协议，其特点是轻量、建议、开放，被广泛应用于物联网(IoT)设备之间的通信。其工作原理大概理解如下：

MQTT协议基于“发布-订阅”模型，其中包括两个角色，发布者（Publisher）和订阅者（Subscriber）。发布者负责发送消息，订阅者则负责接收感兴趣的消息。比如一个非常简单的使用场景：房间里有一个温度传感器，用户需要从远程获取到房间中的温度，则可以将温度传感器配置为MQTT的发布者，并定期发布当前温度的消息，而用户的手机或者电脑作为MQTT的订阅者，订阅温度消息，用户即可得到房间某时某刻的温度信息。

MQTT服务器架设在阿里云的Linux操作系统的轻量型应用服务器上，作为服务的形式不间断运行在服务器的进程中。

上位机使用QT5和C++进行编写，通过移植并调用QT官方提供的MQTT库，编写MQTT的订阅函数，完成上位机对车辆跑动数据的接收和解析显示。

# 硬件开发设计及方案验证

## 3.1 STM32主控引脚资源分配

根据功能需求，使用STM32 CubeMX图形化配置软件为STM32F407ZET6的引脚资源分配如下图所示：



图31 STM32F4芯片引脚分配

根据分配好的引脚导出的Symbol如下图所示：



图32 STM32F407ZET6 Symbol

## 3.2 主机原理图设计

使用嘉立创的国产EDA设计软件：嘉立创EDA（专业版）进行主机原理图的绘制和PCB设计。

### 3.2.1 STM32最小系统电路

STM32F407ZET6芯片的最小电路包括：供电电路、HSE晶振电路、LSE晶振电路、ST-Link下载电路、复位电路。

STM32F407ZET6使用3.3V进行供电，但方向盘整体硬件系统使用5V进行供电，因此需要一路低压差线性稳压器（Low Dropout Regulator）将5V降压为3.3V，在这里使用到了AMS1117线性稳压器，其整体电路如图3-3所示：



图33 STM32主控供电电路

根据STM32F407ZET6的数据手册的推荐HSE电路和LSE电路，我们分别选择使用8MHz的无源晶振和32.768KHz的无源晶振，并绘制原理图如下：

|  图34 HSE电路 |  图35 LSE电路  |
|---|---|

官方提供的ST-Link下载电路引脚较多，默认是使用牛角插座的封装形式，这样的封装非常占用PCB的控件，因此，我将官方提供的参考电路进行了一定简化，删除了不必要的引脚，仅保留主要的信号引脚和复位引脚，这样就节省了PCB的空间，使PCB更小。经过简化后的ST-Link下载调试电路如图3-6所示。

STM32系列芯片复位功能是将相应的GPIO引脚拉低0.5\~3ms左右的时间，即可对芯片重启。根据官方提供的复位电路参考案例，绘制复位电路如图3-7.

|  图36 简化后的下载电路 |  图37 复位电路 |
|---|---|

### 3.2.2 LCD屏幕驱动电路

屏幕驱动电路主要包括三部分：供电电路、屏幕背光电路、主控通信电路。其中，为了保证屏幕工作的稳定性，其供电的3.3V使用独立的LDO进行供电，其供电电路与图3-3相同，不再赘述。

使用的型号为KD035HVFMD145-01的屏幕主控型号为ST7796，与主控STM32的通信方式有SPI和8080两种方式。其中，SPI为三线信号传输，8080支持16线信号传输。ST7796的控制方式由IM0、IM1、IM2三个管脚决定，如下表格为ST7796的控制方式定义。

表31 ST7796控制方式

| IM2 | IM1 | IM0 | 控制方式 |
|-----|-----|-----|---|
| 0 | 0 | 0 | 18Bit 8080 |
| 0 | 0 | 1 | 9Bit 8080  |
| 0 | 1 | 0 | 16Bit 8080 |
| 0 | 1 | 1 | 8Bit 8080  |
| 1 | 0 | 1 | 3-Wire SPI |
| 1 | 1 | 1 | 4-Wire SPI |

因为使用更多的传输线进行数据传输能够增加带宽，提高屏幕的显示效果，因此我们使用16Bit的8080协议进行通信控制。使用STM32的FSMC功能，即可对8080协议进行模拟。因此与屏幕通信的电路如图所示。

这款屏幕的背光为屏幕背光为10颗LED灯珠，可以提供1000尼特的亮度，保证在户外阳光直射下的良好显示效果。其最大驱动电流为40mA，驱动电压为16V，因此需要使用Boost升压电路，将3.3V电压升压为16V。如图为根据厂家提供的设计参考改进的背光驱动电路。

|  图38 LCD控制电路 |  图39 背光驱动电路  |
|---|---|

### 3.2.3 BC260Y模块外围电路设计

BC260Y与STM32主控芯片通过串口进行通信。其主要的外围电路包括：独立的3.3V供电电路、串口电平转换电路、开机复位电路、USIM卡座电路、天线电路。其中3.3V的与上文使用相同方案，即整体电路中一共使用了三路LDO将5V转为3.3V分别给三个不同的模块供电，这里不再赘述。其他电路的设计主要参考移远通信官方提供的硬件设计参考方案，如图3-10所示。



图310 BC260Y参考电路

由于模块的串口电压域为1.8V，而STM32主控的电压域为3.3V，则需在模块和STM32主控之间增加电平转换器，这里我们选择德州仪器的 TXS0108EPWR双向电平转换器，该转换器最高数据速率为60Mbps，具有8个通道，能够满足我们的应用需求。具体电路如图3-11所示。

|  图311 电平转换电路 |  图312 德州仪器TXS0108EPWR |
|---|---|

模块的开机复位电路使用STM32主控的GPIO进行控制，官方推荐使用开集驱动电路来控制RESET引脚。模块上电后，保持RESET及BOOT（即PWRKEY引脚）输入不被拉低，即可实现模块自动开机，开机时序如图3-13所示。

依据官方提供的参考电路，MCU与模块之间的开机和复位控制电路如图3-14所示。

|  图313 BC260Y开机时序 |  图314 开机电路和复位电路 |
|---|---|

USIM卡座电路基于官方提供的参考电路进行设计，外部USIM卡通过模块内部的电源供电，不额外供电，支持1.8/3.0V供电。为了确保良好的ESD防护性能，应当加入ESD保护器件，外部USIM卡座信号走线应从USIM卡座连接到ESD保护器件后再从ESD保护器件连接到模块。完整的电路设计如图。



图315 USIM卡座电路

天线电路如下图所示：



图316 天线电路

### 3.2.4 CAN通信接口设计

STM32主控的CAN_Tx和CAN_Rx引脚与CAN收发器TJA1050的TXD和RXD引脚对应连接，并在CAN_H和CAN_L之间添加120欧姆电阻做CAN总线的阻抗匹配，以保证CAN通信的稳定性。除此之外，TJA1050应使用5V进行供电，在其VCC和GND之间增加100nF电容做滤波。



图317 CAN通信接口设计电路

### 3.2.5 SLM LED电路

SLM模块使用了WS2812B这款LED，其内部集成了处理芯片和3颗不同颜色的LED灯（红，蓝，绿），通过使用单总线协议分别控制不同颜色的亮度强弱，达到全彩显示的目的。每一个灯需要1字节的数据，故一颗WS2812B需要24Bit（3Bytes）的数据。可以采用PWM的方式进行编码，即每个PWM的周期固定为1.25us（800K），占空比为1/3时为0码，占空比为2/3时为1码。WS2812B可以将多个灯珠串联起来，通过一个总线进行控制，将多个灯珠串联后的组合视为队列，在数据传输过程中，前面的灯珠可以将前24Bit的数据留存并解析，剩余的其他数据截断后通过单总线发给线下一个灯珠。使用STM32进行控制可以使用SPI或者TIM/DMA输出PWM的方式进行控制。在本项目中我是用TIM/DMA的方式对WS2812B进行驱动，使用STM32的TIM1定时器的通道1作为信号线对WS2812B进行控制。

SLM模块的作用是根据发动机转速或者电机转速提示车手进行升档降档操作。因此，其灯珠亮灭的个数与发动机转速有关。经过基于成本以及电路驱动能力的考虑，SLM模块使用12颗WS2812B灯珠，其电路如下图所示。



图318 WS2812B电路

### 3.2.6 TYPE-C USB电路

方向盘需要通过USB线缆连接电脑，接收模拟器数据并对模拟器游戏里的车辆进行控制。USB是通用串行总线，是一种快速、灵活的总线接口，硬件上使用D+和D-两个差分信号线进行数据传输。STM32F4系列芯片支持高速USB（USB_OTG_HS）和全速USB（USB_OTG_FS），USB_OTG_HS速率最高为480M Bit/s，但此时需要外接USB HS PHY。USB_OTG_FS最高为12M Bit/s，即1.5Mbytes/s，基本满足项目需求。USB接口选择使用Type-C接口，电路设计如图3-19所示。



图319 USB电路设计

图3-19中，R12和R13两个22欧姆的电阻是高速信号线的终端电阻，其作用是为了阻抗匹配，防止信号回波反射，也有一定的抗击电流的作用。USB_FS_DP管脚处的1.5k欧姆电阻是当设备接入到主机后会被主机识别为全速USB设备。D7为一个ESD芯片，为了防止USB受到雷击或者静电损坏主芯片。

### 3.2.6 其他接口电路

方向盘接入实车和模拟器需要使用线束连接，因此需要预留出线束连接的接插件接口电路。需要预留出的接口线束定义如下表所示：

表32 线束接口定义

| 定义 | 描述 | 类型 |
|---|---|---|
| INPUT8 | 按键输入接口8 | 开关量输入 |
| INPUT7 | 按键输入接口7 | 开关量输入 |
| INPUT6 | 按键输入接口6 | 开关量输入 |
| INPUT5 | 按键输入接口5 | 开关量输入 |
| INPUT4 | 按键输入接口4 | 开关量输入 |
| INPUT3 | 按键输入接口3 | 开关量输入 |
| INPUT2 | 按键输入接口2 | 开关量输入 |
| INPUT1 | 按键输入接口1 | 开关量输入 |
| INPUT9 | 按键输入接口9 | 开关量输入 |
| INPUTA | 按键输入接口A | 开关量输入 |
| CAN_H | CAN高 | 通信接口 |
| CAN_L | CAN低 | 通信接口 |
| USB_FS_DP | USB信号线正 | 通信接口 |
| USB_FS_DM | USB信号线负 | 通信接口 |
| 5V | 5V输入 | 电源接口 |
| GND | 地 | 电源接口 |

将以上线束的接插件进行分组，INPUT1\~INPUT8接口为一组，INPUT9和INPUTA作为换挡拨片开关接口为一组，CAN_H、CAN_L、USB_FS_DP、USB_FS_DM、5V、GND为一组，选型接插件如下图3-20、图3-21、图3-22所示。

|  图320 一组按键接口16PIN接插件 |  图321 二组按键接口4PIN接插件 |  图322 6PIN接插件  |
|---|---|---|

电路原理图如下图所示。



图323 接插件电路原理图

另外预留出Debug接口，如STM32主控芯片的下载调试接口，以及串口电路，方便后期开发过程中进行调试和Debug。选型接口和电路图如下图所示。

|  图324 PZ200-2-04-W |  图325 Debug接口电路 |
|---|---|

## 3.3 PCB Layout设计

原理图设计完成进行DRC检查后将原理图转化到PCB，对PCB进行设计。由于实现功能复杂，为了简化布线布局难度，因此PCB使用四层板，从上到下依次为顶层、内层1、内层2、底层，其中顶层、底层和内层1走信号线，内层2走电源线。最终硬件Layout如下图所示。



图326 PCB Layout



图327 PCB 2D图

使用嘉立创EDA生成PCB的3D预览图如下图。



图328 PCB 3D效果图

PCB上使用到的容阻感原件全部使用0805封装，方便手工使用烙铁进行焊接。经过嘉立创打样后进行焊接，硬件实物如下图。



图329 PCBA实物

经过测试，硬件功能基本正常。

# STM32最小系统基础驱动配置

使用ST官方的STM32 CubeMX图形化代码生成工具对软件上的基础硬件驱动代码进行编写。本章节使用到的全部代码基于STM32官方HAL库。本章节主要介绍本项目中STM32主控固件的HAL层代码设计，包括STM32时钟配置、STM32 SYS模块配置以及数据交互层开发。

## 4.1 时钟配置

STM32的基础硬件配置包括RCC晶振时钟树配置、SYS配置。由于STM32芯片内部自带的时钟（HSI和LSI）在实际工程上使用会导致较大的晶振误差，导致如CAN、USB等需要进行高速通信的外设工作异常，因此我们需要将STM32的默认时钟改为使用外部晶振，来保证功能稳定。硬件上我们使用了8MHz的无源晶振，在STM32 CubeMX的时钟配置RCC菜单中选中时钟源后，将HSI改为HSE，并将晶振频率配置为168MHz，及使芯片在最高频率下运行。时钟树配置如图4-1所示。



图41 STM32 时钟树配置

## 4.2 STM32 SYS配置

为了避免ST-Link下载和Debug功能管脚占用，工程中我们应当在SYS设置中将Debug模式打开选择使用Serial Wire功能。使能Debug后，STM32芯片上的PA13和PA14管脚此时功能定义为SYS_JTMS_SWDIO和SYS_JTCK_SWCLK，防止用户占用这两个引脚用于其他功能导致下载Debug功能异常。

由于项目使用到了FreeRTOS实时操作系统，该系统会占用默认的SysTick为操作系统的始终基准源，该时钟基准源用于实现HAL_Delay()函数以及作为各种timeout的时钟基准，与默认的HAL库时钟基准源冲突，因此我们应当为HAL库选择另外一个时钟基准源。由于TIM1被WS2812B作为信号引脚被占用，因此我们选择TIM2作为HAL库的Timebase Source。修改完成后的SYS设置如下图所示。



图42 SYS设置

## 4.3 数据交互层代码设计

在整体的软件架构中，为了便于上层代码开发及内存管理，提高代码可读性，因此我将应用层使用到的变量、常量、宏定义集中进行定义和声明，在代码工程目录中创建applicationVar.c和applicationVar.h文件，.h文件主要负责对代码中使用到的变量和常量进行声明定义，上层代码开发中只需通过包含该头文件即可对定义好的变量进行调用。.c文件中负责对变量进行初始化，如对结构体进行声明等。



图43 applicationVar.h文件中对变量的声明



图44 applicationVar.c文件中对变量进行定义

# GUI仪表界面开发

## 5.1 HAL层配置

LCD屏幕主控ST7796S使用16Bit 8080协议与STM32主控进行通信。STM32可以通过其自带的FSMC资源模拟8080协议，实现LCD屏幕的驱动。FSMC（Flexible Static Memory Controller）全称为“静态存储器控制器”，支持多种存储器接口和协议，包括SRAM、NOR Flash、PSRAM等等，其中也包括模拟8080时序的LCD屏幕控制。其具有很高的灵活性，STM32的FSMC提供了多种配置选项，可以根据具体的应用需求灵活设置时序和控制信号来适配不同的外部设备接口，通过正确配置FSMC的时序参数，可以模拟8080时序接口的要求。通过使用STM32的FSMC模拟8080时序，可以减少外部逻辑器件的使用需求。传统的8080时序接口通常需要大量的逻辑门和时钟信号生成电路，而使用FSMC可以通过软件配置和控制来模拟这些时序要求。使用FSMC控制器后可以把FSMC提供的FSMC_A[25:0]作为地址线，FSMC_D[15:0]作为数据总线。STM32的FSMC硬件接口和LCD屏幕的硬件电气连接如表4-1所示。

表51 FSMC电气连接

| LCD屏幕信号线 | 描述 | STM32FSMC控制引脚 |
|---|---|---|
| D[15:0] | 数据信号 | D[15:0] |
| RDX | 读数据信号，低电平有效 | NOE |
| D/CX | 数据/命令引脚，高电平为数据引脚 | A[25:0] |
| RESX | 复位信号，低电平有效 | RESET |
| WRX | 写数据信号，低电平有效 | NWE |
| CSX | 片选信号，低电平有效 | NEX |

为模拟8080时序，我们使用STM32的A19引脚与LCD的D/CX连接，当A19拉低表示传输的信号为命令，拉高即为数据。片选信号选择使用NE2，即Bank1的第2区。

根据ST7796S芯片的数据手册得到该芯片的8080协议控制时序参数，并依据STM32F407的主频为168MHz计算后得到，读写时序中各参数应如下所示。



图51 FSMC设置

使用FSMC模拟8080时序，通过控制地址总线即可控制LCD的C/DX数据线是写命令还是数据，C/DX拉低表示为命令，拉高表示为数据。STM32F4对于16BBit位宽的地址总线会进行右移操作，比如使用地址A0时会使用Bit1，Bit0位被跳过。因此，在项目中我们使用到的A19引脚被拉低时，其写入的地址数值为0x000FFFFE(0111 1111 1111 1111 1111 0111)。根据硬件连接使用到的NE信号线，与Bank对应区域的地址进行或运算，即可写入读取信号。如下图为STM32的Bank地址对应关系。我们使用A19，NE2，故LCD屏幕寄存器的基地址为0x64000000 \| 0x000FFFFE。



图52 BANK地址

FSMC配置完成后使用CubeMX生成代码，完成HAL层功能开发。

## 5.2 BSP层开发

BSP层的主要功能是通过调用HAL层接口代码完成对LCD屏幕的读写寄存器、读写GRAM功能的开发，并基于此完成LCD屏幕的基本初始化、画点功能、颜色填充功能等功能的开发。

首先在bsp_LCD.h中对LCD的重要参数集进行定义，这里我们使用C语言中的结构体对一部分变量进行定义，如涉及到LCD屏幕宽度、高度等数据，以及坐标指令等。代码如图5-3和5-4所示。

|  图53 LCD重要参数集定义 |  图54 LCD寄存器和GRAM地址映射结构体 |
|---|---|

FSMC对8080时序进行模拟，通过写地址的形式对LCD读写时序进行模拟，根据硬件连接，对LCD对应FSMC内存基础地址进行定义，其中0x64000000为Bank1.Sector2的起始地址，0x000FFFFE是A19的偏移量。有了以上定义，LCD写命令、数据会很方便。通过宏定义LCD_WRITE_REG、LCD_WRITE_DATA、LCD_READ_DATA函数，对读写数据和命令功能进行定义。代码如图5-5所示。



图55 LCD相关宏定义

基于以上定义，对读写寄存器和数据函数进行编写，以写寄存器函数为例，LCD_WriteReg()函数具体实现如图所示。



图56 LCD写寄存器函数

通过编写好的读写寄存器等功能函数，修改厂家提供的屏幕驱动代码，编写LCD屏幕的初始化函数。该函数主要负责通过写入寄存器指令对LCD上电启动后的电源设置、颜色格式设置、GAMMA设置等初始化操作， 如图为初始化函数中的部分代码。



图57 LCD初始化代码（部分）

基于读写寄存器函数、写GRAM函数等功能函数，我们能够在屏幕上显示我们想要显示的内容，如画点、填充颜色等操作。如下图为在指定区域填充指令颜色块的函数定义。此函数也是后期我们移植LVGL的绘制接口函数，LVGL对界面图形的绘制主要基于该函数功能。



图58 LCD_Color_Fill()函数定义

至此，我们完成了LCD屏幕驱动BSP层的基本功能开发。通过在main()函数中调用LCD_Init()对LCD屏幕进行初始化，while(1)循环中使用LCD_Clear(uint16_t color)函数对屏幕进行清屏操作，即可进行屏幕显示测试。如下图为屏幕测试显示效果。



图59 屏幕纯色显示效果

## 5.3 APP层——LVGL开发

仪表界面使用开源的GUI框架LVGL进行开发。LVGL具有免费开源、轻量化、支持部件丰富、硬件接口丰富等特点，非常适合本项目使用的STM32F4主控平台。同时，其具备有丰富的资料，官方文档对各个API接口都有着详尽的描述和相应的参考案例。另外，LVGL官方提供的SquareLine Studio工具可以极大简化设计工作。项目中使用的LVGL版本为8.3.3。

### 5.3.1 LVGL移植

LVGL官方文档中有STM32平台移植LVGL的详细说明，因此主要依据官方文档对LVGL进行移植。LVGL移植的前提是已经具备有完整的屏幕显示驱动程序，前文中已经完整叙述了HAL层和BSP层对屏幕显示驱动的开发过程。

基于创建好的已经具备有完整驱动显示程序的工程对LVGL进行移植工作。首先在LVGL的官方仓库克隆完整的版本为8.3.3代码，下载的代码内容如图5-10。需要我们复制到工程中的代码主要是examples/porting下的所有文件、src文件夹、lv_conf.h、lvgl.h和demo文件（用来验证LVGL移植是否成功）。src目录下的文件为LVGL的源码，src目录中的代码如图5-11所示。Porting目录下为LVGL移植文件的模板代码，包括基本的显示驱动接口、文件系统驱动、外设接口驱动代码。移植到工程后我们需要将该目录下代码文件名中的”_template”后缀删除，如图5-12所示。Demo目录下主要是LVGL官方提供的一些测试例程，通过在LVGL的相关代码文件里使能相关宏定义即可运行官方示例代码。移植Demo目录是为了方便我们移植完毕后对移植效果进行检验，测试无误后在实际项目工程中会将相关代码删除，并关闭相关宏定义的使能。Demo目录下的代码如图5-13所示。

|  图510 LVGL完整仓库代码 |  图511 LVGL源码 |
|---|---|
|  图512 porting目录文件  |  图513 demo目录文件  |

将代码移植到STM32的工程目录中，移植后的工程目录如图所示。其中ui_design文件夹下为项目工程中实际使用到的UI设计文件和逻辑代码。



图514 移植后的LVGL代码目录

将相关代码文件添加到STM32的工程中，包括src目录下的core相关所有代码文件(core)、draw目录下的所有代码文件和其sw目录下的所有文件(draw)、extra目录下的所有文件（包括该目录下的所有子目录下的代码文件）(extra)、font目录下所有的文件(font)、hal目录下的所有.c文件(hal)、misc目录下的所有文件(misc)、widgets目录下的所有代码(widgets)，以及porting目录下的disp.c、fs.c、indev.c三个文件(porting)，最后添加LVGL的配置文件lv_conf.h和lvgl.h(config)和demo例程。添加后的代码目录如下图5-15所示。



图515 STM32 LVGL工程目录结构

将代码添加到工程中后，依据实际工程中使用的硬件进行移植修改。修改lvgl_conf.h文件中相关代码，如设置颜色格式为RGB565（依据代码注释将LV_COLOR_DEPTH修改为16），修改默认的显示刷新周期为10ms（LV_DISP_DEF_REFR_PERIOD默认为30ms）。将LV_USER_PREF_MONITOR和LV_USE_MEM_MONITOR使能设置为1来打开LVGL运行界面的FPS帧率显示和内存占用显示，方便后期调试进行仪表界面运行效率的优化。

在lv_port_disp.c和.h文件中，依据实际的硬件对显示接口代码进行编写。如图5-16所示修改屏幕的分辨率为480\*320。在lv_port_disp_init()接口函数中使用第一种定义缓存的方式即使用单缓存数组（节省RAM内存），将源代码中的Example1相关代码取消注释，并依据实际分辨率更改数组大小，如图5-17所示。修改disp_init()函数，调用BSP_LCD.c中定义的LCD_Init()代码，实现LVGL的硬件初始化代码修改，如图5-18所示。最后修改disp_flush()屏幕界面渲染更新函数，调用bsp_LCD.c中定义的LCD_Color_Fill()函数，如图5-19所示。即可完成显示接口的修改。



图516 lv_prot_disp.c分辨率设置



图517 定义显示数据缓存方式



图518 LVGL硬件初始化代码修改



图519 disp_flush()函数

完成以上修改后，LVGL的移植工作基本完成。通过在lvgl_conf.h中使能相关demo宏定义，如LV_USE_DEMO_WIDGETS宏定义使能为1，并在main函数中调用lv_init()、lv_port_disp_init()和lv_demo_widgets()函数对lvgl和Widgets Demo进行初始化，while(1)中调用lv_task_handler()，即可运行官方例程，对移植工作的效果进行验证，验证效果如图所示。



图520 LVGL例程运行效果

### 5.3.2 LVGL界面设计

仪表界面使用LVGL官方提供的SquareLine Studio软件进行设计。根据车手在驾驶时的习惯，我们需要在仪表上显示的内容包括：发动机（电机）转速、车速、挡位、圈速时间、剩余油量（剩余电量）、车辆错误码等信息。[10]其中，车手相对关注比较多的数据是车速、转速、挡位信息，因此，这些数据在界面中应当被着重显示，在UI设计中尽量突出重点。使用SquareLine绘制UI如图5-21。



图521 UI界面设计

设计的UI界面主要分为两个Screen：Startup页面和Home页面。当程序启动时，首先会显示Startup界面，该界面中的Bar进度条自行4000ms的更新动画，动画结束后进入Home页面。Home页面显示有车速、转速、挡位、圈速、发动机（电机）温度、控制器温度、油量（SOC）等信息。

通过SquareLine软件对绘制好的界面进行预览和仿真后，即可导出相应的.c和.h文件，添加到STM32工程中的LVGL/UI中进行调用，即可在STM32上进行显示。STM32平台显示效果如图5-22所示。



图522 STM32实机UI显示效果

# 实车数据采集功能开发

项目基于凌云车队2020赛季大学生方程式油车凌云Ⅷ号赛车进行实车功能开发和测试。凌云Ⅷ号赛车采用MoTeC M800 ECU，整车数据通信方式采用CAN通信，CAN波特率为1Mbps。整车CAN网络拓扑如图所示，CAN网络中CAN ID使用标准ID。



图61 凌云Ⅷ号整车CAN拓扑

## 6.1 CAN通信HAL层配置

STM32F407主控具备有两路CAN，我们使用其中一路。基于STM32 CubeMX对CAN通信进行基础配置，在软件界面中使能CAN，并依据波特率对Prescaler、Time Quanta Bit Segment 1、Time Quanta Bit Segment 2、ReSynchronization Jump Width参数进行配置。这些参数与波特率的关系式如下：

Baud Rate = APB1 peripheral clocks / (Time Quanta in Bit Segment 1 + Time Quanta in Bit Segment 2 + ReSynchronization Jump Width) / Prescaler

依据实车CAN网络波特率，我们需要将其配置为1Mbps波特率，已知STM32F407 APB1总线频率为42MHz，故取Time Quanta in Bit Segment 1为3，Time Quanta in Bit Segment 2为3，ReSynchronization Jump Width为1，Prescaler为6时，STM32的CAN1波特率为1Mbps。

其他参数配置如时间触发模式、自动唤醒模式等保持CubeMX软件的默认配置。打开CAN接收中断，使用中断方式对接收到的CAN报文进行处理。故HAL层配置结果如图6-2和6-3所示。

|  图62 CAN基本参数设置 |  图63 CAN中断配置 |
|---|---|

以上通过STM32 CubeMX生成代码，完成了CAN通信的基本HAL层配置。

## 6.2 CAN通信BSP层配置

完成HAL层开发后，基于HAL层接口在bsp_CAN.c和bsp_CAN.h中对CAN通信的BSP层进行代码开发。CAN通信的BSP层主要实现STM32的CAN过滤器设置、CAN报文发送功能开发。

首先在bsp_CAN.h中声明CAN收发报文结构体变量，其为静态结构体变量，不可被外部文件调用。声明如图6-4所示。CAN_TxHeaderTypeDef和CAN_RxHeaderTypeDef具体定义在stm32f4xx_hal_can.h中，其定义如图6-5和6-6所示。



图64 CAN收发报文结构体

|  图65 CAN_TxHeaderTypeDef定义 |  图66 CAN_RxHeaderTypeDef定义 |
|---|---|

CAN收发过滤器配置采用32位宽的掩码模式，不过滤任何CAN ID，及对接收ID的所有位都不做屏蔽，因此设置FilterMaskIdHigh 和FilterMaskIdLow都为0x0000。将通过ID的CAN报文存储到FIFO0中。CANFilter_Config()代码如图6-7所示。



图67 CANFilter_Config()函数

CAN发送报文功能需要软件配置好要发送报文的ID类型、CAN ID、传送报文的帧类型和数据长度。在整车CAN网络中，我们使用标准数据帧，方向盘仅发送数据帧，数据长度为8 Bytes。使用软件查询的方式对CAN报文进行发送。故CAN1_Send()函数如图6-8所示。



图68 CAN1_Send()函数

## 6.3 CAN APP层代码开发

CAN通信APP层主要实现整车报文数据解析、方向盘按键事件响应功能开发，基于BSP层，在CAN_app.c和CAN_app.h中对功能进行实现。

整车报文数据解析功能实现的主要思路是依据MoTeC M800 ECU发送的数据报文格式进行解析，将相关物理量如车速、发动机转速等读取到在applicationVar.h中定义的racingCarData结构体中，APP层其他平行的应用如LVGL中通过racingCarData结构体将读取到的物理量进行使用。如图为racingCarData结构体定义。



图69 racingCarData结构体定义

如图6-9中结构体油车MoTeC相关变量定义，我们主要接收的数据有机油温度、机油压力、节气门开度、氧传感器数据、ECU控制器温度、挡位、发动机温度以及基本的前轮车速和发动机转速。由于凌云Ⅷ号车未搭载前轮轮速霍尔传感器，故实际上我们无法获取到前轮轮速数据，进而无法得知准确的车速参考。为了便于测试，我们车速的实际数据来源是通过发动机转速和变速箱传动比及车辆大小链轮齿比计算得来的后轮轮速，在不考虑后轮打滑的情况下，该车速具备有一定的参考价值。

MoTeC M800一共输出4种格式各不相同的CAN报文，分别针对Dash（如CDL3等）、VCP/PDM、SLM、PLM。其中针对Dash发送的数据最为全面。根据MoTeC M800 ECU Manager我们可以得到这组CAN报文为0x5F0。M800 ECU上电以后会持续不断的在整车CAN网络发送报文，其发送频率可以在M800 ECU Manager中进行配置，默认为每秒50组CAN报文。其每组CAN报文的长度为144字节，由于CAN总线自身限制，每组报文需要分18帧进行发送，每帧报文8字节，即8 x 18 = 144字节。依据MoTeC官方的M800 CAN协议文档，我们可以得知，每组CAN报文的最后一帧的最后的第五、第六、第七字节为固定的0XFC、0XFB、0XFA，我们可以通过这三个字节判断每组CAN报文的结束帧。依据MoTeC官方提供的CAN协议文档，我们需要得到的物理量与实际CAN报文关系如表所示。

表61 M800 CAN协议

| 字节序号 | 物理量 | 单位 |
|---|---|---|
| 0:1 | 发动机转速 | 1RPM |
| 2:3 | 节气门开度 | 0.1% |
| 8:9 | 发动机温度 | 0.1℃ |
| 10:11 | 氧传感器信号 | 0.001La |
| 24:25 | 机油温度 | 0.1℃ |
| 44:45 | 低压电池电压 | 0.01V |
| 46:47 | ECU温度 | 0.1℃ |
| 104:105  | 挡位 | 1 To 1  |

依据CAN协议编写CAN解析代码，并在CAN接收中断中对解析函数进行调用，当收到CAN报文进入接收中断后，则进行CAN报文解析。如图6-10为CAN报文解析代码。



图610 CAN报文解析函数

在CAN接收中断函数中，由于MoTeC的CAN报文为多组报文，因此需要在接收完一整组共18帧CAN报文后才能对数据进行处理，如图6-11为CAN接收中断函数中处理该业务逻辑的代码。



图611 CAN接收中断接受多组CAN报文并解析逻辑代码

另外，除了兼容凌云Ⅷ号燃油方程式赛车，我们还对凌云Ⅸ号赛车的CAN协议进行了兼容。如图6-12为解析凌云Ⅸ号赛车CAN协议的代码，其原理在此不做赘述。



图612 凌云Ⅸ号赛车CAN报文解析函数

方向盘按键处理功能基于CAN通信，其工作流程为，当检测到车手按下按键后，方向盘会在整车CAN网络中发送CAN ID为0X155的CAN报文，方向盘一共有10个按键接口，对应CAN报文的10Bit数据，从按键0\~按键9对CAN报文中的Byte0\~Byte1中16个Bit的前10Bit依次置1。CAN网络中其他控制器只需通过关注相应数据位对要实现的功能进行响应即可。其具体代码实现如图6-13所示。



图613 按键处理函数

# 模拟器相关功能实现

模拟器相关功能中的模拟器数据采集基于Simhub软件实现。Simhub是一款用于模拟器赛车游戏的数据抓取工具，该软件的基础功能免费且部分开源，具有详尽的Github技术文档，支持多种竞技类游戏，如神力科莎系列、F1系列等市面上常见的模拟器游戏；同时支持多种传感器和设备，方便用户DIY模拟器游戏相关外设；支持多种输出方式，提供给用户更多选择的方式。

基于STM32的USB外设，我们将方向盘虚拟为一组复合的USB设备，分别是虚拟串口和HID游戏手柄设备，分别实现数据采集功能和游戏控制器功能。

## 7.1 模拟器功能HAL层开发

在STM32 CubeMX软件中使能USB FS功能，同时配置USB外设时钟树的相关频率为42MHz。使能完成后，CubeMX配置界面如图7-1所示。



图71 USB功能HAL配置

## 7.2 模拟器功能BSP层开发

USB复合设备开发基于Github中alambe94开源的I-CUBE-USBD-Composite配置工具。该项目作为软件包配合STM32 CubeMX进行使用，能够非常快速地配置USB复合设备。通过Clone项目到本地，并在CubeMX软件中安装、使能该软件包，即可进行使用。如图7-2为USB Composite功能配置界面，使能了CDC_ACM设备和HID_MOUSE设备，在代码生成后，通过基于MOUSE修改其设备描述符，将HID_MOUSE设备更改为HID_JOYSTICK设备实现游戏控制器功能。



图72 USB Composite配置界面

完成配置后生成代码。此时编译工程并将代码烧录到STM32，使用USB将方向盘PCBA接入到计算机后，会被识别为一路USB串口设备和一路鼠标设备。

在生成的usbd_cdc_acm_if.c代码中，修改CDC_Receive()函数，该函数为虚拟串口接收中断函数。当虚拟串口接收到串口数据后会进入该中断进行数据处理。由于STM32的虚拟串口的缓冲区大小有限仅为256Bytes，故当串口数据超过256字节时会造成数据的丢包。因此我们需要在程序上进行循环队列缓冲，在接收数据时先将数据放入到缓存区，直到接收到字符串的结束符完成一组串口数据的接收。修改后的CDC_Receive()函数如图7-3所示。



图73 CDC串口接收中断函数

修改HID_MOUSE相关代码文件中的设备描述符部分，首先修改配置描述符，将原来代码中声明的MOUSE设备修改为NONE设备，代码如图7-4所示。



图74 配置描述符修改

修改USB设备的设备描述符如图7-5所示。



图75 JOYSTICK设备描述符代码

最后修改usbd_desc.c中对复合设备的描述相关代码如下图。



图76 USB复合设备定义

修改完成后编译工程，将代码烧录到硬件并通过USB线缆连接到计算机，方向盘即可被识别为虚拟串口设备和JOYSTICK设备，如图7-7和7-8所示。

|  图77 USB虚拟串口设备 |  图78 USB控制器设备 |
|---|---|

游戏手柄的按键读取功能定义在Bsp_USB_Composite.c中。其按键读取功能代码如图7-9所示。



图79 USB按键读取功能函数

此时使用windows控制面板中的游戏控制器校准窗口，即可对方向盘上的按键功能进行测试。如图所示。

|  图710 设备管理器手柄设置 |  图711 设备管理器手柄按键校准测试 |
|---|---|

## 7.3 模拟器相关功能APP层

APP层主要实现模拟器数据接收功能的数据栈协议。Simhub采集模拟器游戏数据后将数据通过JavaScript脚本打包为json字符串，通过虚拟串口将打包好的json报文发送给方向盘，方向盘根据json报文进行解析即可获取模拟器游戏内车辆跑动的物理量。Simhub打包json脚本的JavaScript代码如图7-12所示。其接收到的数据以结构体形式保存，类似CAN通信功能中定义的racingCarData结构体，在applicationVar.c中我们也定义了一个sh_CarData的结构体。



图712 Simhub打包json字符串脚本及打包好的字符串

其打包好的json字符串形式为：

{"speed":0,"rpm":4000,"cLapTime":"00:55.92","gear":"N","bLapTime":"00:00:00","fuel":53,"redLineRPM":17900,"brake":0,"throttle":0,"lap":1}

STM32的APP层通过移植的开源json库cJson的相关代码，即可对接收到的json字符串进行解析。



图713 JSON报文解析函数

# 无线数传功能开发

## 8.1 HAL层开发

无线数传基于移远通信的BC260Y-CN模块[11]，是一款低能耗高性能的NB-IoT模块。通过3GPP Rel-13和3GPP Rel-14无线电通信协议与网络运营商的基础设备建立通信。该模块在方向盘硬件中通过串口与STM32主控进行通信，其默认的串口通信波特率为9600bps，为了保证满足单位时间内上传报文的数据吞吐量，在项目中我们需要提高其与STM32主控之间的通信波特率到460800bps。因此，HAL层开发主要配置STM32与BC260Y相连接的USART3串口，并开启串口的相关中断。HAL层配置如图8-1和8-2所示。

|  图81 串口波特率配置 |  图82 打开串口中断 |
|---|---|

生成代码后，在生成的串口HAL相关代码中添加printf()函数重定向代码，将printf()重定向到串口，方便后期调试工作进行串口调试。本项目中一共使用了两路串口USART1和USART3，USART3与BC260Y连接进行通信，USART1用于与电脑通信进行调试输出。因此，printf()函数中定义了两路串口打印输出，用户可通过usartTxFlag变量控制printf()函数输出的是哪一路串口，当usartTxFlag = 1时则使用串口1进行打印输出，usartTxFlag 为其他值时使用串口3进行打印输出。其代码如图8-3所示。



图83 串口重定向函数

## 8.2 BC260Y BSP层开发

BC260Y的BSP层主要进行对APP层发送AT指令的字符串和接收到的BC260Y的串口回显数据进行处理，其中包括cmdToBC260Y函数、BC260Y_init函数和串口接收中断函数。

cmdToBC260Y函数为发送AT指令给BC260Y并判断是否有效的函数。其定义为：

uint8_t cmdToBC26Y(char \*strSource, char \*strTarget, uint8_t okCheck);

其中，strSource为AT命令字符串。strTarget为若AT指令BC260Y成功响应后发送回的字符串。okCheck为是否进行模块回调字符串包含”OK”字符，因为一些AT命令发送给模块后回显命令仅”OK”两个字符，这类情况需要单独进行处理。若BC260Y回显字符串中包含成功响应后需要检查的strTarget，则返回1，否则返回0。该操作会重复五次，若超过五次均为响应成功则判断超时，直接return 0处理。该函数的具体代码如图8-4所示。



图84 cmdToBC260Y函数

BC260Y_init()函数为BC260Y模块初始化函数。其通过在上电后拉低模块的RST引脚进行短暂复位操作后对模块进行开机操作。BC260Y开机后会自动尝试联网操作，若联网成功，会通过串口返回当前的IPV4地址，字符串形如：“IP: 192.168.10.226”。如果联网不成功，未返回带有“IP”字符的字符串，则初始化操作失败，此时应当检查BC260Y的硬件是否错误，如天线连接是否异常或SIM卡是否未插。IP连接成功后会进行SIM卡检查、关闭休眠模式、查询信号质量等操作，这些信息会通过串口1打印到调试人员的电脑上。初始化代码如图8-5所示。



图85 BC260Y初始化函数

串口接收函数主要业务逻辑是将BC260Y的回显命令字符串进行初步处理。因为BC260Y的回显字符串格式上较为难以处理，因此需要将其中的部分不必要的字符如”\\r”等进行删除操作。同时在接收中断中会有如MQTT服务器连接是否成功等回显字符串的判断，若判断成功将相应的标志位进行置1。为了避免数据溢出，会在代码中加入memset函数对缓存数组中的数据处理完毕后进行清空。代码如图所示。



图86 串口接收中断

## 8.3 BC260Y APP层开发

STM32主控对BC260Y基于其官方定义的AT指令进行通信。如下表格列举了在本项目中使用到的AT指令及其描述。

表81 AT指令表

| AT指令 | 用途 | 返回值 |
|---|---|---|
| AT\\r\\n | 测试指令 | OK or Error |
| AT+CIMI\\r\\n | 查询有卡无卡 | 460xxxxxxxxx or ERROR |
| AT+CSQ\\r\\n | 查询信号质量 | +CSQ:22,0 or +CSQ:99, 99 |
| AT+CGATT?\\r\\n | 查询网络连接 | +CGATT:1 or +CGATT:0 |
| AT+QSCLK?\\r\\n | 配置休眠模式 | OK |
| AT+IPR = 460800\\r\\n | 配置波特率为460800 | OK |
| ATE0\\r\\n | 关闭命令回显 | |
| AT+QMTOPEN=0,”MQTT.Server”,1883\\r\\n | 打开MQTT服务器 | OK +QMTOPEN:0,0 |
| AT+QMTCONN=0,”BC260Y”,”User”,”passwd”\\r\\n | 连接MQTT服务 | OK +QMTCONN: 0,0,0 |
| AT+QMTPUB=0,0,0,1,"hello",11,"hello world"\\r\\n | 发布消息 | OK |

STM32主控启动BC260Y的流程如图所示。APP层主要依据BC260Y的BSP层接口进行开发，其代码主要在MQTT_App.c和MQTT_App.h中。在BC260Y初始化成功后，会进行MQTT服务的打开并连接服务器。项目中使用到的MQTT服务器基于阿里云的轻量应用型服务器进行搭建，基于开源的MQTT消息代理Eclipse Mosquitto，其实现了基于MQTT 3.1协议版本和3.1.1版本的轻量、适用于低功耗NB-IoT设备的完整服务器软件架构。通过在服务器部署并配置Mosquitto Server，放行云服务器的MQTT相应1883端口，即可完成对服务器的搭建。



图87 BC260Y运行流程

MQTT_App.c中主要定义了以下功能函数：mqttServiceStartup()、MQTT_Init()、jsonPack()和MQTT_Pubdata(char \*json)。其中，mqttServiceStartup()函数使能串口中断，并调用BSP层的BC260Y_init()函数和APP层的MQTT_Init()函数，并依据BC260Y_init()函数的返回值和MQTT_Init()函数的返回值操作PCBA上预留的两个LED进行亮灭，方便调试人员在不连接串口的情况下了解网络和MQTT连接状况，若二者都初始化成功，则PCB上的两颗LED全部亮起。MQTT_Init()函数和mqttServiceStartup()函数分别如图8-8和8-9所示。



图88 MQTT_Init()函数



图89 mqttServiceStartup()函数

MQTT_Pubdata(char \*json)函数是将打包好的json字符串经过与BC260Y的发布消息AT命令“AT+QMTPUB”字符串进行组合后通过串口发送给BC260Y模块。其代码实现如图所示。



图810 MQTT_Pubdata(char \*json)函数

jsonPack()函数是将实车跑动数据进行json打包函数，通过sprintf()函数，将从实车CAN网络中解析得来的车速、转速等信息打包到json0[]数组中。打包好后，通过MQTT_Pubdata(char \*json)函数将json字符串发送给服务器。其具体代码如图8-11所示。



图811 jsonPack()函数

图8-11中json0[]具体定义如下：

json0[]="{\\"cSpeed\\": %d,\\"Pos\\": %d,\\"bAlarm\\": %d,\\"lmSpeed\\": %d,\\"rmSpeed\\": %d,\\"bTemp\\": %d,\\"bLevel\\": %d,\\"gMode\\": %d,\\"cMode\\": %d,\\"lmTorque\\":%d,\\"rmTorque\\":%d,\\"batVol\\": %d,\\"carDistce\\": %d,\\"mcu1Temp\\": %d,\\"mcu2Temp\\": %d,\\"brakeTravel\\": %d,\\"lmoTemp\\": %d,\\"rmoTemp\\": %d}";

## 8.4 无线数传测试

完成STM32上的无线数传功能开发后，使用我在凌云车队2020赛季开发的无线数传上位机进行数据接收测试。该无线数传上位机基于QT5进行开发，能够进行MQTT服务器消息订阅，显示订阅消息数据等功能。如图8-12为其部分后端MQTT消息解析代码。



图812 无线数传上位机代码

将PCB板接入到实车后进行数据上报测试，打开无线数传上位机，其数据显示效果如图8-13所示。基本完成了无线数传显示的开发。使用MQTT Dashboard APP订阅MQTT相关服务器和Topic即可实现在手机上实时查看车辆跑动数据，如图8-14和8-15为安卓手机的MQTT Dashboard APP现实的实车跑动数据。



图813 无线数传显示界面

|  图814 MQTT Dashboard APP实车跑动数据显示界面A |  图815 MQTT Dashboard APP实车跑动数据显示界面B |
|---|---|

# SLM功能模块开发

SLM（Shift LED Module）为换挡提示模块，其作用在于依据当前发动机转速点亮LED灯提示车手进行升档降档操作。硬件上使用了WS2812B作为LED，其具有亮度高、单线控制、支持全色彩显示的特点。

## 9.1 SLM HAL层开发

硬件上使用STM32的TIM1 CH1的PWM输出接口作为12个WS2812B的信号线接口，使用DMA进行PWM输出。WS2812B使用PWM方式进行编码，即每个PWM的周期固定为1.25us，即800K，占空比为1/3时为0码，2/3时为1码，复位信号为80个周期的低电平，即不低于50us的低电平。电气连接上，WS2812B的特点是多个灯珠串联，通过一个总线控制多个灯珠，总线上的数据传输时时，将属于自己的24Bit数据留下，余下的向下一个灯珠进行传递。24Bit数据中，第一字节为Green，第二字节为Red，第三字节为Blue。连接方法如图所示。



图91 WS2812B电气连接方法

通过CubeMX对TIM1进行配置，使能TIM1，开启Channel1的PWM输出通道，选择Clock Source为Intrernal Clock。WS2812B驱动需要800K的PWM波输出，STM32的TIM1挂载在APB2总线，其频率为168MHz，因此，168 \* 1000 / 800 = 210，故Counter Period 设置为209（210-1），配置如图9-2所示。另外打开TIM1的DMA通道，使用DMA方式驱动PWM波形可以节省STM32的CPU资源，能够保证输出波形的效率和稳定性。修改内存到外设及数据宽度为半字节。如图9-3所示。

|  图92 TIM1配置 |  图93 TIM1 DMA配置 |
|---|---|

## 9.2 SLM BSP层驱动开发

BSP层基于HAL层的接口函数进行开发，主要实现WS2812B的亮灯操作，包括设置灯珠颜色、点亮灯珠个数、WS2812B初始化功能。首先通过宏定义将WS2812B的灯珠个数、单个灯珠数据长度、0码占空比、1码占空比、复位周期数等控制参数进行定义，如图9-4所示。



图94 WS2812B控制参数宏定义

定义WS2812B的RGB颜色控制函数，其函数定义为：

void ws2812_set_RGB(uint8_t R, uint8_t G, uint8_t B, uint16_t num);

该函数通过指针指向静态变量RGB_buffur[]数组，该数组是存储WS2812B颜色数据的数组，外部调用该函数时将传入的R、G、B形参存储到RGB_Buffer中，再通过DMA方式发送，控制PWM的占空比，即可控制灯珠的颜色。其函数具体定义如图9-5所示。



图95 ws2812_set_RGB函数

定义WS2812B的初始化函数，ws2812_init(uint8_t led_nums)，通过该函数对12颗LED灯珠进行初始化操作。设置12颗灯珠全部熄灭。其函数实现如图9-6所示。



图96 ws2812_init()函数

另外还有设置指定个数灯珠为纯蓝色、纯红色、纯绿色的函数，其代码结构与init函数一致，不做赘述。

## 9.3 SLM APP层开发

基于BSP层的对WS2812B灯珠基本的功能函数对APP层进行开发。在SLM_App.c中，定义了RPM_LED_Shine()函数。该函数通过判断当前是模拟器连接还是实车连接，自行选择数据来源，模拟器连接的情况下，依据sh_CarData结构体中的rpm决定亮灯个数；实车模式连接的情况下则依据racingCarData结构体中的rpm决定亮灯个数。当发动机转速达到换挡时机要求的转速时，灯珠会全部亮起并进行闪烁。除此之外还有一个待机模式，即方向盘在没有任何连接的情况下，全部蓝灯会亮起。其函数实现如图9-7所示。



图97 RPM_LED_Shine()函数

在FreeRTOS的进程中对RPM_LED_Shine()函数进行调用，SLM显示效果如图9-8、9-9、9-10所示。

|  图98 模拟器SLM显示效果 |  图99 待机模式显示效果 |  图910 实车SLM显示效果 |
|---|---|---|

# 总体功能整合

基于预期的总体软件架构，最上层使用FreeRTOS对前文所涉及到的所有功能进行整合。FreeRTOS是一个开源的实时操作系统，项目中我们使用STM32 CubeMX对FreeRTOS系统进行配置。

## 10.1 系统功能启动逻辑设计

为了实现兼容实车和模拟器的所有功能，我们需要对所有功能进行整合。主要功能分为两组，一组为实车模式功能，另外一组为模拟器模式功能。其中，两个模式共用同一个仪表界面进行数据显示。实车模式的功能包括：CAN通信数据采集、无线数传、控制器功能。模拟器模式的功能包括：Simhub数据采集、控制器功能。综上所述，设计功能启动流程如图10-1所示。



图101 系统总体启动流程

系统启动后首先进入待机模式，即SLM全部LED为蓝色的状态，此时等待数据接收。若接收到实车CAN通信数据，则SLM的所有LED熄灭，进入实车模式；若接收到Simhub发送的串口json报文，则SLM的所有LED熄灭，进入模拟器模式，模拟器模式开启后，同时会启动基于USB JOYSTICK的控制器功能。实车功能启动后，会尝试启动无线数传的相关功能，并开启圈速计时器，按键控制器响应车手按下按钮的事件并发送相应的CAN报文。

## 10.2 FreeRTOS 进程配置



图102 FreeRTOS进程配置

如图所示，一共创建有6个进程，分别是LVGL_Task、LVGL_Meter_Task、LVGL_Lap_Timer_Task、Iot_Upload_Task、BC260Y_Init_Task、RPM_LED_Task；其优先级自上而下依次降低。LVGL的相关进程优先级最高，为osPriorityRealtime2和osPriorityRealtime1，因为LVGL的相关进程负责仪表界面的更新显示，对实时性要求高，因此需要抢占更高的优先级，优先使用CPU资源。同时根据LVGL官方文档对实时操作系统上推荐的使用方式，申请了一个Mutex进程锁，当LVGL使用CPU时，其他无关进程无法占用CPU资源，来保证LVGL的稳定运行。LVGL_Task中主要进行lv_task_handler()，该进程为LVGL的主进程。LVGL_Meter_Task进程为LVGL仪表界面数据更新进程，通过获得racingCarData数据和SH_carData数据，对仪表界面的显示进行实时更新。LVGL_Lap_Timer_Task进程为实车模式下圈速计时器更新进程，该计时器的时间更新使用TIM3定时中断进行数据更新，未使用LVGL的心跳函数，因为LVGL的心跳函数由于FreeRTOS的介入导致计时不准确，因此额外使能了一路硬件定时中断。

另外三个较低优先级的进程，BC260Y_Init进程为实车模式下4G模块初始化进程，该进程通过osEventFlag getCarData事件标志位进行控制，在方向盘收到CAN报文进入CAN接收中断函数后，CAN接收中断函数内部会发送相应的标志位，BC260Y_Init进程被启动。BC260Y初始化成功后，会启动Iot_Upload_Task进程，开启无线数传数据上报，同样，该进程也受到和BC260Y_Init进程一样的标志位getCarData控制，只有接收到CAN报文并成功解析后才会进行数据上报。RPM_LED_Task为SLM相关功能进程，该进程受getCarData的第二Bit位控制，当CAN接收到报文或串口接收到Simhub的Json报文后，会将getCarData的相应bit位置1，启动RPM_LED_Task进程，此时SLM的LED退出待机模式，进入相应的模式根据转速进行亮灭。

经过调试，以上进程均正常运行。总体功能调试完毕，方向盘软件开发工作基本完成。整体工程对STM32F407芯片的整体资源占用情况如图所示。



图103 IDE编译器输出的编译信息

已知STM32F407ZET6的可用FLASH为512KB，可用RAM为128KB，程序编译完毕后，根据编译信息可知，程序的RAM大小为RW-data和ZI-data的总和，约为125.8KB，FLASH大小为Code和RO-data的总和，约为256KB，程序的FLASH使用情况约为STM32主控的50%，RAM使用情况约为98%。程序所使用的RAM已经接近STM32F407的RAM容量上限。

# 总结

## 11.1 方向盘机械结构设计

方向盘外形轮廓延续凌云车队五号车的方向盘盘面轮廓进行设计，该方向盘盘面轮廓符合大学生方程式系列赛事的方向盘相关规则。装配方式上，采用比较常见的三明治结构进行装配。总体机械结构采用AutoDesk的Fusion 360软件进行设计。方向盘整体主要分为握把、屏幕固定板、3.5inch屏幕、顶壳、边缘外壳、PCBA、底壳、快拆器、换挡总成等部分。盘面整体尺寸长为254mm（10inch），宽为170mm，总体高度63mm（不包括快拆器）。其中，边缘握把、屏幕固定板、边缘外壳、换挡机构总成部分使用树脂材料进行光固化打印加工制造，方向盘的上顶壳、底壳、换挡总成的拨片使用3mm厚度的斜纹碳纤维板进行CNC加工制造。方向盘3D模型渲染如图所示。

|  图111 方向盘外观 |  图112 方向盘正面 |
|---|---|
|  图113 方向盘背面 |  图114 方向盘侧视图  |

所有零件外包进行加工，加工完成后装配实物如图所示。



图115 方向盘实物

## 11.2 功能测试

方向盘通过快拆器能够适配大学生方程式赛车油车和电车，同时也支持部分加装有快拆器花键的模拟器底座。该项目基于凌云车队2020赛季凌云Ⅷ号赛车进行测试，模拟器功能基于罗技G27模拟器和神力科莎游戏进行测试。为了将实车模拟器适配到罗技G27，需要设计一个转接座固定快拆器花键，如图11-6为设计的转接座，图11-7为通过该3D打印的转接座将方向盘连接到模拟器进行测试的照片。

|  图116 快拆器转接座 |  图117 方向盘连接模拟器测试 |
|---|---|

经过测试，方向盘仪表能够正常显示实车和模拟器跑动数据，按键的控制按键也能实现对实车和模拟器的控制功能。如图11-8为在实车环境进行测试的照片，实车测试时为雨天，方向盘经过实车连续三小时的跑动测试，所有功能依然保持正常。经过车手的反馈，方向盘的仪表显示效果优秀，数据更新及时，且换挡等操作顺畅。



图118 方向盘实车测试

无线数据传输方面，在户外赛车跑动条件下，BC260Y的延迟仅为100\~200ms，丢包率极低。如图为无线数传上位机对实车跑动数据进行实时显示。



图119 无线数传上位机实时显示跑动数据

## 11.3 待改进之处

本项目的初衷在于能够抛砖引玉，希望国内大学生方程式系列赛事上，各家参赛车队能够在数据采集和分析上有更多的创新，因为跑动数据无论是对于赛车的调教还是对于车手的个人提升都有着很大的作用。以这个方向盘作为一粒种子，希望后面有更多志同道合的人加入到数据采集功能开发的行列中来，能够在这个项目的基础上开发出更多更加强大的功能。本项目从硬件到软件再到机械结构设计为独立开发，并于2023年1月份基于GPL-3.0开源协议开源在了github平台上。本文对本项目的后期发展还有许多想法，希望在未来有足够的技术能力去进行实现。

在第十章节对方向盘操作系统内容的描述中提到了软件对STM32主控的RAM占用过多的问题，基于F4平台开发的相关内容在其芯片资源和性能的限制上已经显得非常捉襟见肘，因此需要对方向盘的软件进行优化，尽量减小RAM的占用。或者更换主控平台，选择性能更加强大的其他STM32芯片，如H7系列等。

功能上，预期设计时设计有外部的16Mbytes Flash芯片，但是由于后期开发过程中发现STM32的RAM资源紧张，而没有对相关功能进行完整开发。但是在工程代码里能够看到已经导入了FATFS相关的代码。希望后期在解决RAM占用问题后，能够开发FATFS数据缓存功能，可将实车数据实时保存到外部的Flash中，并生成.csv文件或者MoTeC I2软件可识别的数据。另外为了增强产品的兼容性和应用场景，希望后期可以增加通过导入DBC文件适配新的实车CAN通信协议的功能，方便其他用户快速将产品运用到新的车辆。基于使用到的BC260Y模块，充分利用硬件性能，希望能够添加OTA升级功能，通过阿里云平台，能够在线升级STM32主控固件，方便用户进行系统更新和调试。

硬件上，BC260Y模块的天线设计在初期一直存在天线附近PCB上覆铜的问题，虽然不影响使用，但是优化后应该会有更好更稳定的效果。另外，硬件PCBA为了方便用烙铁进行手工焊接，容阻感元器件全部使用了0805封装，比较占用PCB的空间，因此希望后期可以通过贴片技术进行PCBA的焊接，这样可以选择使用更小的容阻感元件，进而优化整体PCB的布局和走线，进一步缩小PCB的尺寸。在CAN通信接口设计上，当前设计并未考虑比较严峻的电磁干扰环境，因此未对CAN模块接口做防护设计。后期希望能通过增加光电隔离电路和电源隔离设计增强CAN通信接口的抗干扰性能。

目前开发的所有方向盘功能其实只是冰山一角，数据采集功能能够正常使用后，后期优化的工作重点应当在于数据的分析和处理。因此，方向盘的上位机功能就显得尤为重要。以方向盘作为数据采集的基础，其采集到的数据必然要放到其他平台进行详细的数据分析。对上位机功能的设想如下：

首先，上位机支持多个平台，支持Android、windows电脑、Linux计算机。可以方便用户和工程师全天候的对数据进行监控和分析。上位机具备有方向盘硬件配置功能，能够通过上位机给方向盘导入新的车辆适配协议，对方向盘的CAN波特率进行配置、按键功能自定义，甚至对方向盘仪表界面的显示数据内容进行更改。上位机还应具备最基本的无线数据接收和显示的功能，对离线数据的读取可以类似于MoTeC系列产品，方向盘接入到上位机后自动读取离线缓存的跑动数据。支持界面配置功能，用户可以通过widget控件的方式，在上位机界面中增加或删除数据分析的窗口。

以上，就是目前对本项目的未来开发方向的想法。项目伊始，本文就秉持着做产品的态度对这款方向盘进行设计，希望这个项目未来能够有更多的人加入进来，能够愈加完善，国内大学生方程式赛场上的车辆数据采集分析从硬件到软件不再被国外垄断，甚至可以做的比国外更好。

# 参考文献

>   [1]中国大学生方程式赛事规则-2022[Z].

>   [2]Suspension Subsystem for ZER-20 Fall 2019 – Spring 2020 Advisor: Dr. Deckler[Z].

>   [3] Z. Wang and S. Wang, "Design of Steering Wheel and Magnetic Shift Mechanism of FSAE Racing Car," 2021 7th International Symposium on Mechatronics and Industrial Informatics (ISMII), Zhuhai, China, 2021, pp. 146-150, doi: 10.1109/ISMII52409.2021.00037.

>   [4] Shanay Shah, Ravi Satasia, Gautam Patel. Design of 3D Printed Steering Wheel for FSAE Vehicle[J]. International Research Journal of Engineering and Technology (IRJET),2020,2395:56-72

>   [5]Almeida, Vitor Fernandes de. “Electronic Steering Wheel for FST car.” (2009).

>   [6]陈斌,施伟,魏垂浩,解国林.基于CAN总线和STM32的FSAE赛车控制与显示系统设计[J].数字技术与应用,2021,39(11):169-172.DOI:10.19695/j.cnki.cn12-1369.2021.11.54.

>   [7]许燕.基于stm32的电动汽车仪表系统设计关键技术[J].内燃机与配件,2020(19):26-27.DOI:10.19475/j.cnki.issn1674-957x.2020.19.012.

>   [8]周明.恶劣电磁环境中的CAN总线接口电路设计[J].单片机与嵌入式系统应用,2012,12(12):31-33.

>   [9]邢洋,李立伟,张洪伟.基于STM32单片机的CAN总线分析仪的设计[J].青岛大学学报(工程技术版),2013,28(01):19-21.DOI:10.13306/j.1006-9798.2013.01.010.

>   [10]陈建国,甘永超,王保华.FSC赛车无线通讯智能仪表的设计与开发[J].汽车科技,2014(01):1-4.

>   [11]吴纪铎,刘爱松,赵梦海.T-BOX车载网联终端设计[J].汽车零部件,2022(02):11-16.DOI:10.19466/j.cnki.1674-1986.2022.02.003.

>   [12]张翔,陈雨人.研究型汽车驾驶模拟器有效性确认研究[J].交通信息与安全,2011,29(02):63-68.

>   [13]王捷,马咏梅,刘新田,束振,陈赵勤.电动方程式赛车动力总成的仿真与试验验证[J].汽车工程师,2021(06):21-24+42.

>   [14]SIMHUB.WIKI.SimHub gernal.[EB/OL].（2023-02-15）[2023-03-15].

# 致 谢

感谢当年的自己因为凌云车队选择了河北工程大学，感谢大学生方程式赛事给我带来了如此充实快乐的四年。非常幸运，能够在车队遇到一群志同道合的朋友，能一起造车，一起为相同的事情欢喜忧愁。很喜欢F1车手卡罗尔·史密斯的一句话：“胜利通常是以牺牲娱乐时间作为代价的。不过对于赛车，不管你从哪个角度看它都会觉得像是在玩儿一样。”为了能让我们的车能够落地，能在赛场上比其他学校的车更快，我们所做的一切都像是在玩儿一样，看到自己的设计从想法变成现实，通过集思广益给赛车带来了一点点的性能或是稳定性的提升，从把趴窝的活爹修复成别人眼里帅气的赛车，这都带给我很强的成就感。车队的经历让我热爱上了赛车，每当听到引擎的轰鸣，轮边电机的电流声，还有加工车间切割机打磨车架钢管的噪音，都会激发我内心对速度的渴望，让我觉得这是可以让我投入一生的事业。

感谢毫末智行科技保定分公司的同事，尤其是梁蛟龙、吕东等同事在我实习的过程中给我提供了很多帮助，在这里我不但精进了自己原来在车队学习到的技术能力，吕工和梁工还为我拓宽了自己的技术栈，在实习过程中带我接触到了整车诊断、FBL等新的技术；梁工在我毕设的设计过程中提供了很多设计的方向思路和硬件优化方案，为我拓宽视野，是我未来职业发展中的良师益友。

感谢凌云车队的同僚和学弟，周鑫、王梓帆、温彭杰、徐晨、刘荣骏、行益康等学弟直接参与到了项目的调试和测试工作中，对本项目的开发、测试等工作中提供了很多帮助，在方向盘的优化方向上提供了很多建设性意见，在此一并表示感谢。感谢神一样的凌云Ⅷ号赛车，感谢科信的周鑫、王梓帆、温彭杰等兄弟们把八号车修复如初，为方向盘测试提供了一个非常优秀的平台。

本项目使用到的硬件物料如PCB打样、电子元器件采购等，由嘉立创平台赞助提供。本项目共打样5个版本的PCB，其中包括两个版本的使用了六层板工艺的PCB。元器件采购上，嘉立创为本项目提供了赞助支持，全部元器件都是免费获得的。从项目立项到结项，嘉立创为本项目提供了大概价值三千元人民币的物料支持。本项目的硬件设计也同样全部基于嘉立创EDA专业版软件进行设计。嘉立创提供的优质的打样服务很大程度上加快了我的开发进度。非常感谢嘉立创对项目的赞助和支持！

最后，感谢自己在2D155的室友：张泽晨，袁帅旺，孙玉龙，很幸运能够遇到你们。大学四年时光如白驹过隙，仿佛第一次来到155宿舍还是在昨天，初次见面时的场景历历在目。大学中几乎所有的美好回忆都与你们有关，再次感谢。

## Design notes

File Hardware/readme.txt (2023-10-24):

完整硬件工程请前往嘉立创硬件开源平台获取：
https://oshwhub.com/nolimy/steeringWheel_project

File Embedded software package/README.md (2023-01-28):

# streeringWheel_MeterBox_STM32_withOS
基于STM32F407ZET6的大学生方程式赛车仪表，集成无线数传功能，使用LVGL图形库。
🚧🚧🚧正在施工🚧🚧🚧

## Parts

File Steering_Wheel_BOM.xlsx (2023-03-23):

物料 |  | 个数 | 描述 | 单价(RMB) | 合计(RMB) | 链接 | 备注
CNC | 顶板 | 1 |  | 150 | 150 |  | 自行加工
 | 底板 | 1
 | 左拨片 | 1
 | 右拨片 | 1
小计 |  |  |  |  | 150
3D打印 | 拨片主体 | 2 | 使用黑色树脂材料打印 | 400 | 400 |  | 自行加工
 | 拨片连杆 | 2
 | 左上握把 | 1
 | 左下握把 | 1
 | 右上握把 | 1
 | 右下握把 | 1
 | 屏幕固定板 | 1
 | 边缘外壳 | 1
小计 |  |  |  |  | 400
紧固件 | M3*22 铜柱 | 12 | 固定顶板和底板 | 2.5(10个) | 5 | https://detail.tmall.com/item.htm?abbucket=15&id=542213588710&ns=1&skuId=3258324297350
 | M3*15 铜柱 | 4 | 固定PCB | 3.2(20个) | 3.2 | https://detail.tmall.com/item.htm?abbucket=15&id=542213588710&ns=1&skuId=3258324297350
 | M3*10 圆头螺栓 | 17 | 底板固定和屏幕固定板固定 | 3.1（50个) | 3.1 | https://detail.tmall.com/item.htm?abbucket=5&id=694131607161&rn=b4c1d11afca624925c0b1c19fd125620
 | M3*10 沉头螺栓 | 7 | 顶板固定 | 3.4(50个) | 3.4 | https://detail.tmall.com/item.htm?id=693377485791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
 | M3*8 圆头螺栓 | 8 | PCB固定 | 3.1(50个) | 3.1 | https://detail.tmall.com/item.htm?abbucket=5&id=694131607161&rn=b4c1d11afca624925c0b1c19fd125620
 | M3*10内六角螺栓 | 4 | 拨片基座安装孔 |  |  | https://detail.tmall.com/item.htm?abbucket=5&id=694131607161&rn=b4c1d11afca624925c0b1c19fd125620
 | M3*14内六角螺栓 | 4 | 拨片本体安装孔 | 4(50个) | 4 | https://detail.tmall.com/item.htm?id=694131607161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
 | M5*30平头内六角螺栓 | 2 | 拨片转轴孔 | 5.6(50个) | 5.6 | https://detail.tmall.com/item.htm?id=694131607161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
 | M2*12内六角螺栓 | 4 | 拨片微动开关安装孔 | 5.7(50个) | 5.7 | https://detail.tmall.com/item.htm?id=636175026159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
 | M2螺母 | 4 | 拨片微动开关固定 | 2.3(200个) | 2.3 | https://detail.tmall.com/item.htm?id=534459768753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
 | M3螺母 | 8 | 拨片本体固定&&拨片基座固定 | 2.3(200个) | 2.3 | https://detail.tmall.com/item.htm?id=534459768753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
 | M5螺母 | 2 | 拨片转轴固定 | 4.5(200个) | 4.5 | https://detail.tmall.com/item.htm?id=534459768753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
小计 |  |  |  |  | 42.2
配件 | 12mm按钮 | 8+2 |  | 1.2 | 12 | https://item.taobao.com/item.htm?id=630776716481 | （红色&绿色）
 | OMRON SS-5微动开关 | 2+1 | 拨片微动开关 | 10.64(3个) | 10.64 | https://item.taobao.com/item.htm?id=664863617743
 | 磁铁M10*3mm | 多个 | 拨片磁铁 | 9.5(10个) | 9.5 | https://item.taobao.com/item.htm?id=567580325565&ns=1&abbucket=15 (https://item.taobao.com/item.htm?spm=a230r.1.14.84.66b32d44J3jom6&id=567580325565&ns=1&abbucket=15)
 | 4mm * 11.7mm导光柱 | 12 | LED导光 | 6.5(10个) | 13 | https://item.taobao.com/item.htm?id=606143459177&ns=1&abbucket=10
 | 弹簧线 | 2 | 实车线束及模拟器线束 | 26 | 52 | https://m.tb.cn/h.UNSGeut?tk=zjKOd6I4gZe
 | USB接口 | 1 | 模拟器USB接口 | 2.1(5套) | 2.1 | https://detail.tmall.com/item.htm?abbucket=15&id=14422856956&ns=1&skuId=5053017858253
 | GX16-7 公母航空插头 | 4 | 线束用 | 1,2 | 4.6 | https://detail.tmall.com/item.htm?abbucket=12&id=42107248347&ns=1&skuId=74722507319
小计 |  |  |  |  | 103.84
杂项 | 导线 | 若干 |  | 63.4 | 63.4 | https://detail.tmall.com/item.htm?abbucket=15&id=41296905861&ns=1&skuId=3741986177674
 | 屏幕KD035HVFMD145-01 | 1 | 高亮度屏幕 | 95 | 95 |  | 联系17331234849
 | PCBA | 1 |  | 219.89 | 219.89
 | 热缩管 | 若干 |  | 7.25 | 7.25 | https://detail.tmall.com/item.htm?id=586569031072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
小计 |  |  |  |  | 385.54
总计 |  |  |  |  | 1081.58

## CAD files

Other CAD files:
Hardware/Datasheet/BC260Y-CN/03 Hardware/Quectel_BC260Y-CN_2D_Dimensions_V1.0/Quectel_BC260Y-CN_2D_Dimensions_V1.0.dwg
Hardware/Datasheet/LCD/KD035HVFMD145-01.dwg

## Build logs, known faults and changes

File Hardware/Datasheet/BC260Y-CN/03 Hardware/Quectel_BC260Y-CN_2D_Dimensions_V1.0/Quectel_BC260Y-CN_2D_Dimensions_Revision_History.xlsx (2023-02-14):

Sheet: Title Page
BC260Y-CN
2D Dimensions Revision History
NB-IoT Module Series
BC260Y-CN_2D_Dimensions_Revision_History
Date: 2022-07-06
Status: Released

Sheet: Foreword
At Quectel, our aim is to provide timely and comprehensive services to our customers. If you require any assistance, please contact our headquarters:
Quectel Wireless Solutions Co., Ltd.
Building 5, Shanghai Business Park Phase III (Area B), No.1016 Tianlin Road, Minhang District, Shanghai 200233, China
Tel: +86 21 5108 6236
Email: info@quectel.com
Or our local office. For more information, please visit:
http://www.quectel.com/support/sales.htm
For technical support, or to report documentation errors, please visit:
http://www.quectel.com/support/technical.htm
Or email to: support@quectel.com
Legal Notices
We offer information as a service to you. The provided information is based on your requirements and we make every effort to ensure its quality. You agree that you are responsible for using independent analysis and evaluation in designing intended products, and we provide reference designs for illustrative purposes only. Before using any hardware, software or service guided by this document, please read this notice carefully. Even though we employ commercially reasonable efforts to provide the best possible experience, you hereby acknowledge and agree that this document and related services hereunder are provided to you on an “as available” basis. We may revise or restate this document from time to time at our sole discretion without any prior notice to you.
Use and Disclosure Restrictions
License Agreements
Documents and information provided by us shall be kept confidential, unless specific permission is granted. They shall not be accessed or used for any purpose except as expressly provided herein.
Copyright
Our and third-party products hereunder may contain copyrighted material. Such copyrighted material shall not be copied, reproduced, distributed, merged, published, translated, or modified without prior written consent. We and the third party have exclusive rights over copyrighted material. No license shall be granted or conveyed under any patents, copyrights, trademarks, or service mark rights. To avoid ambiguities, purchasing in any form cannot be deemed as granting a license other than the normal non-exclusive, royalty-free license to use the material. We reserve the right to take legal action for noncompliance with abovementioned requirements, unauthorized use, or other illegal or malicious use of the material.
Trademarks
Except as otherwise set forth herein, nothing in this document shall be construed as conferring any rights to use any trademark, trade name or name, abbreviation, or counterfeit product thereof owned by Quectel or any third party in advertising, publicity, or other aspects.
Third-Party Rights
This document may refer to hardware, software and/or documentation owned by one or more third parties (“third-party materials”). Use of such third-party materials shall be governed by all restrictions and obligations applicable thereto.
We make no warranty or representation, either express or implied, regarding the third-party materials, including but not limited to any implied or statutory, warranties of merchantability or fitness for a particular purpose, quiet enjoyment, system integration, information accuracy, and non-infringement of any third-party intellectual property rights with regard to the licensed technology or use thereof. Nothing herein constitutes a representation or warranty by us to either develop, enhance, modify, distribute, market, sell, offer for sale, or otherwise maintain production of any our products or any other hardware, software, device, tool, information, or product. We moreover disclaim any and all warranties arising from the course of dealing or usage of trade.
Privacy Policy
To implement module functionality, certain device data are uploaded to Quectel’s or third-party’s servers, including carriers, chipset suppliers or customer-designated servers. Quectel, strictly abiding by the relevant laws and regulations, shall retain, use, disclose or otherwise process relevant data for the purpose of performing the service only or as permitted by applicable laws. Before data interaction with third parties, please be informed of their privacy and data security policy.
Disclaimer
a) We acknowledge no liability for any injury or damage arising from the reliance upon the information
b) We shall bear no liability resulting from any inaccuracies or omissions, or from the use of the information contained herein.
c) While we have made every effort to ensure that the functions and features under development are free from errors, it is possible that they could contain errors, inaccuracies, and omissions. Unless otherwise provided by valid agreement, we make no warranties of any kind, either implied or express, and exclude all liability for any loss or damage suffered in connection with the use of features and functions under development, to the maximum extent permitted by law, regardless of whether such loss or damage may have been foreseeable.
d) We are not responsible for the accessibility, safety, accuracy, availability, legality, or completeness of information, advertising, commercial offers, products, services, and materials on third-party websites and third-party resources.
Copyright © Quectel Wireless Solutions Co., Ltd. 2022. All rights reserved.

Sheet: Revision History
Version | Date | Author | Description
- | 2022-07-06 | Winks WANG | Creation of the document
1.0 | 2022-07-06 | Winks WANG | First official release

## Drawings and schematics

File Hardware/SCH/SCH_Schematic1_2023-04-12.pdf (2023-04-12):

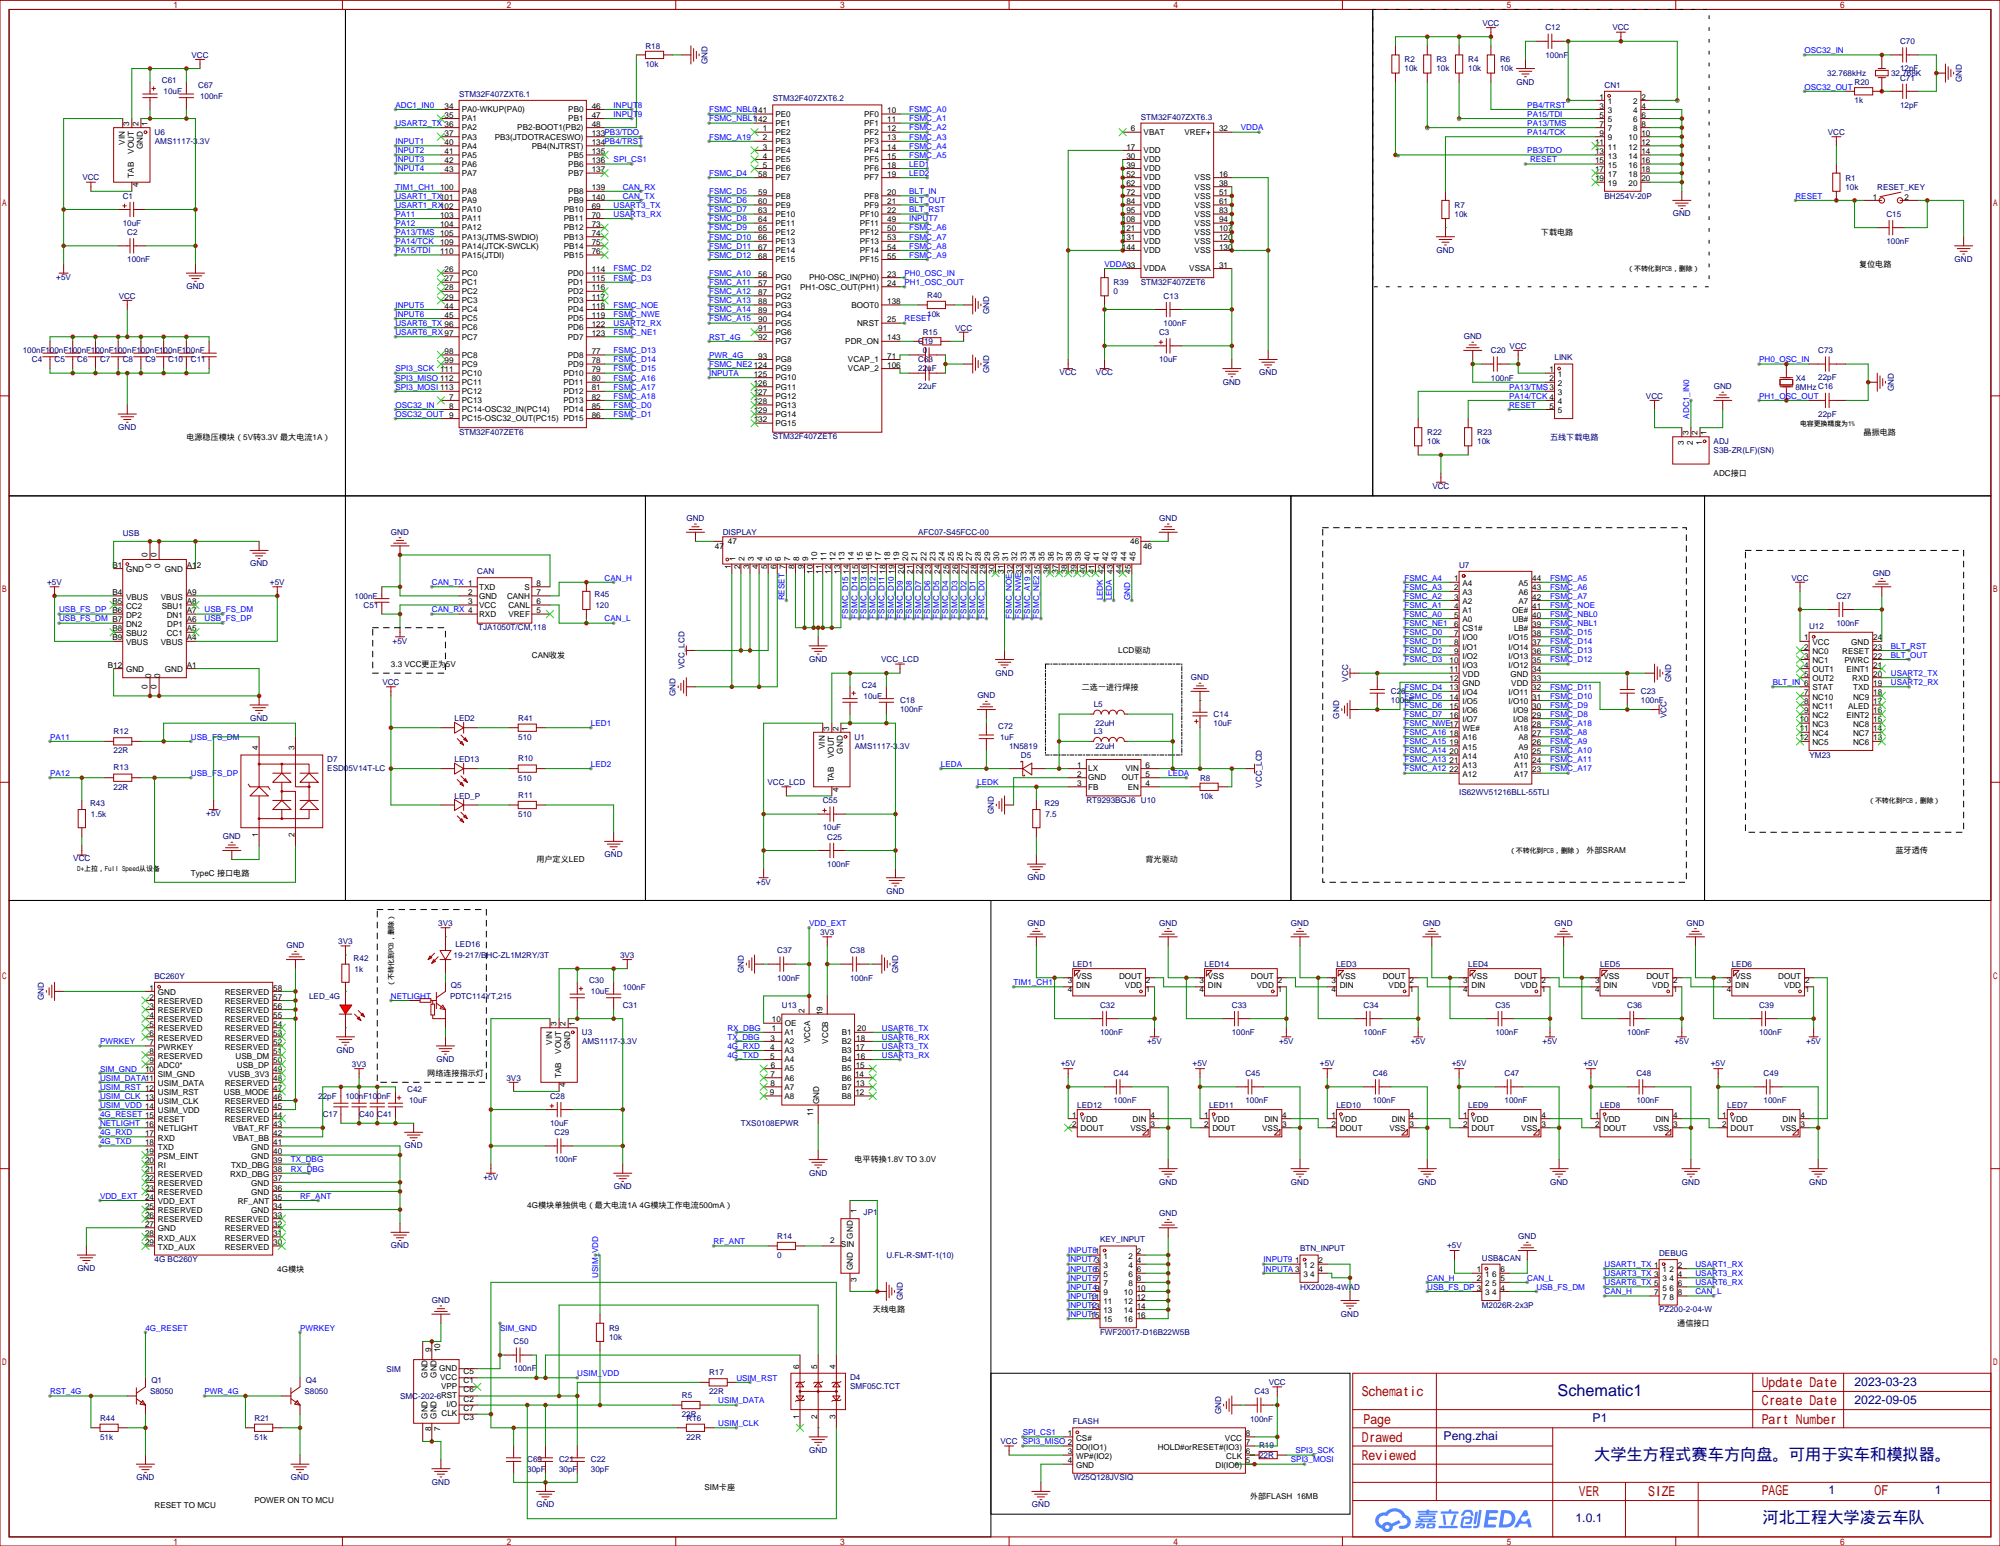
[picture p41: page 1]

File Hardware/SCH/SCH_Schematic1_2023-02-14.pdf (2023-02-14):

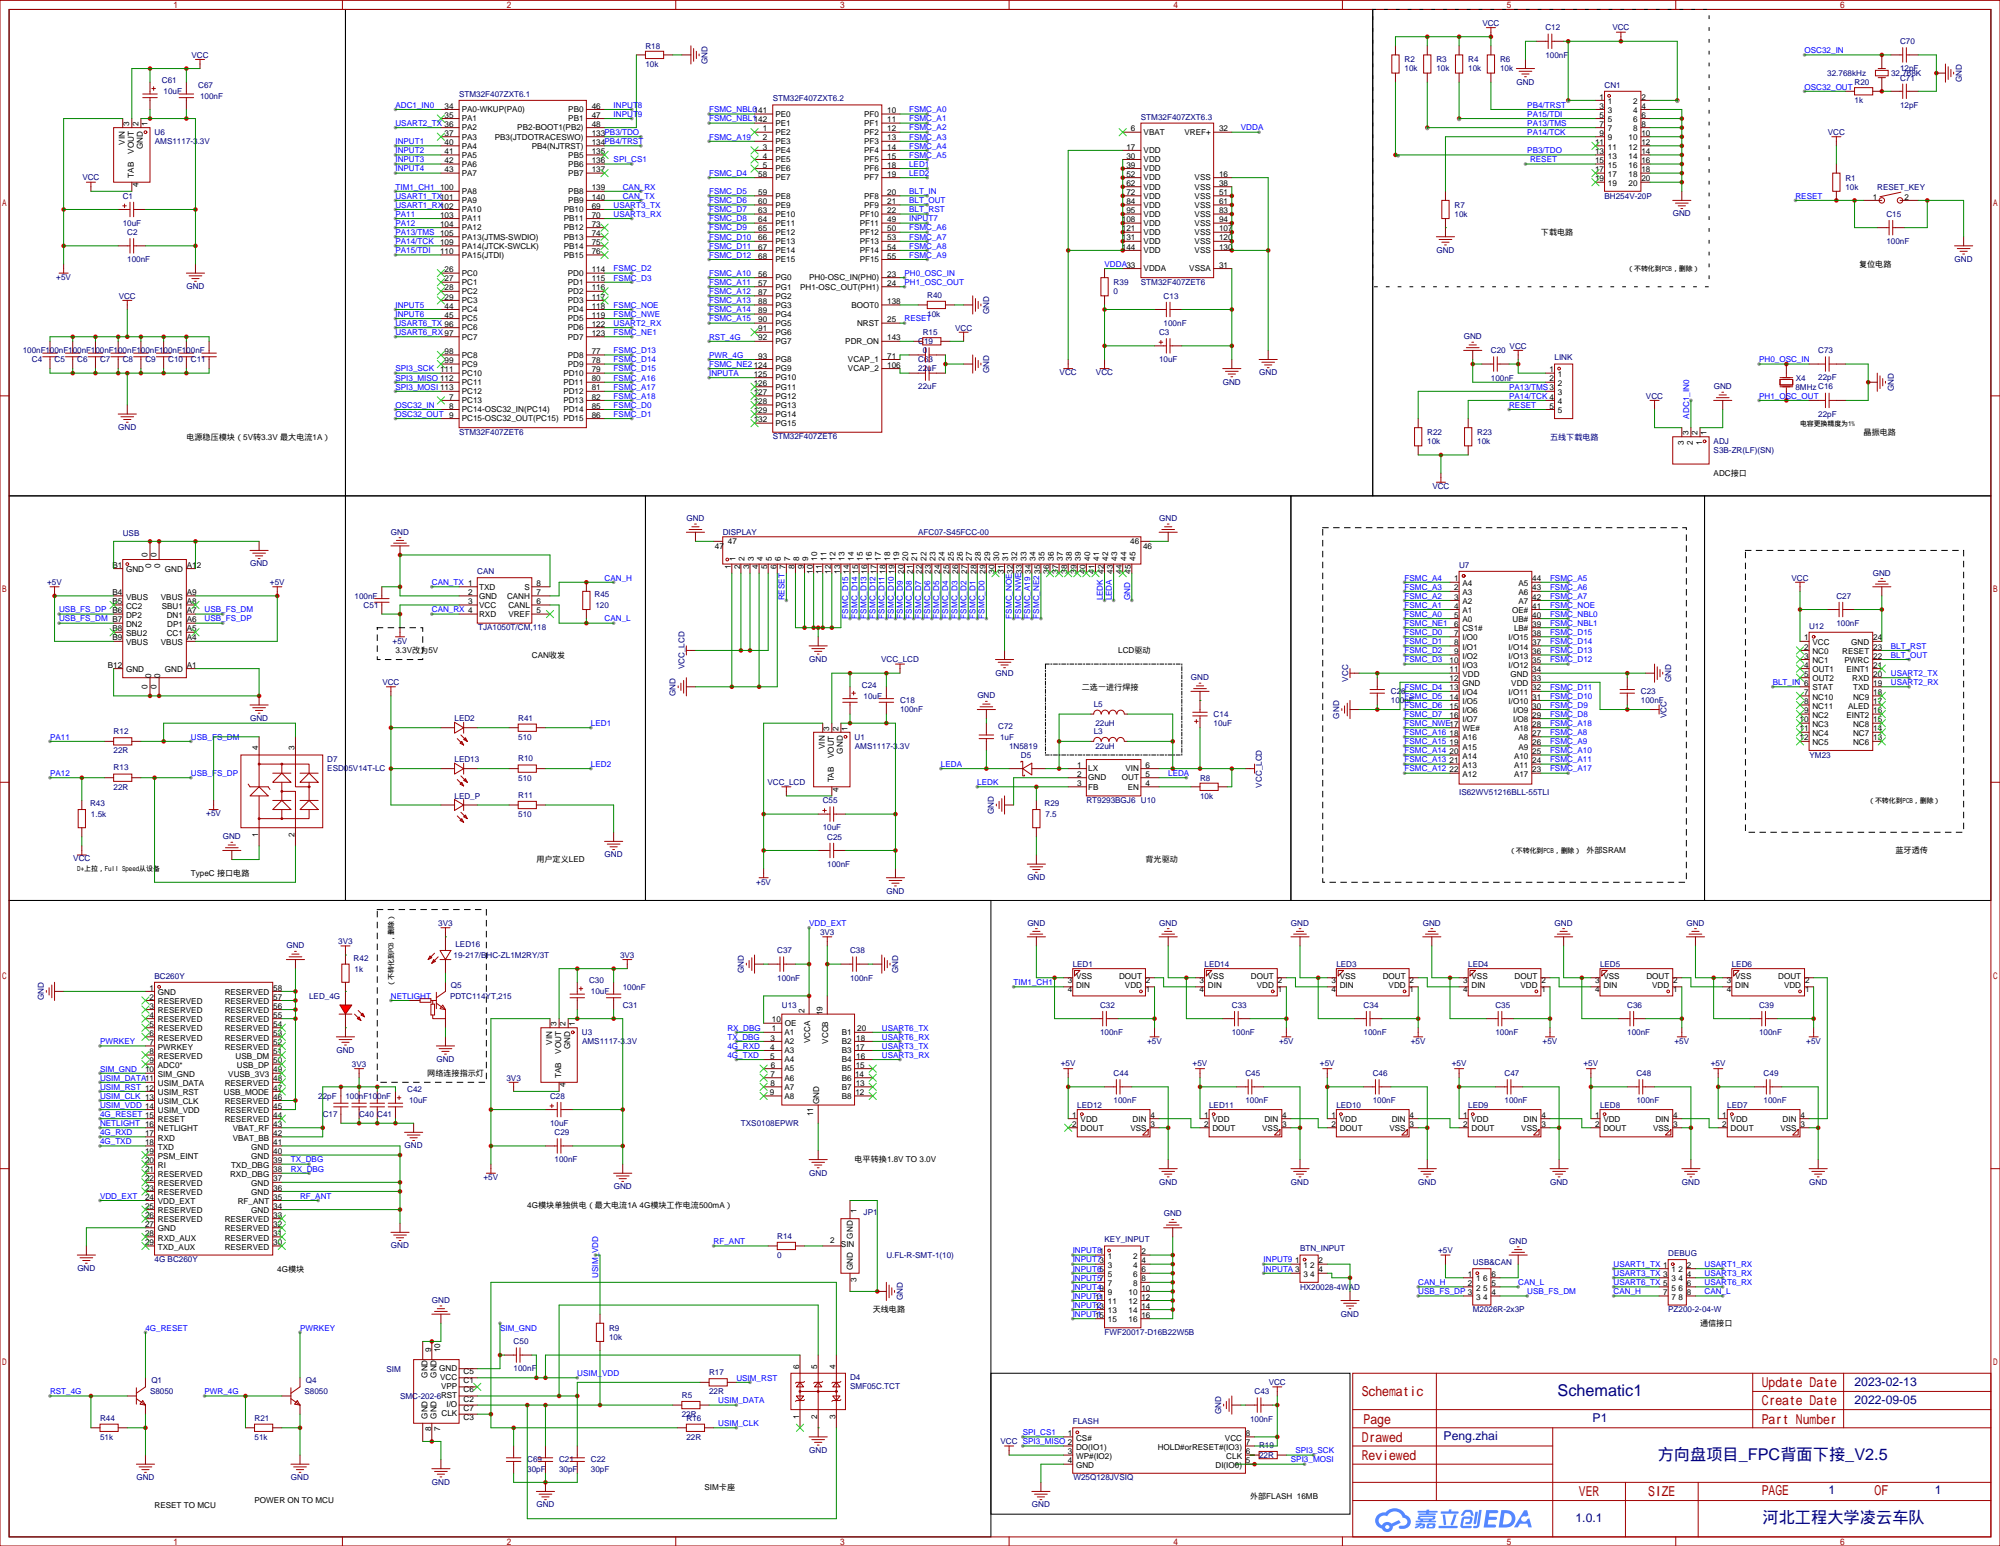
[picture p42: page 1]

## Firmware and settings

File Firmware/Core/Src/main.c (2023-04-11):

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
/* Includes ------------------------------------------------------------------*/
#include "main.h"
#include "cmsis_os.h"
#include "can.h"
#include "crc.h"
#include "dma.h"
#include "spi.h"
#include "tim.h"
#include "usart.h"
#include "usb_otg.h"
#include "gpio.h"
#include "fsmc.h"

/* USER CODE BEGIN Includes */
#include "bsp_LCD.h"
#include "bsp_BC260Y.h"
#include "bsp_WS2812B.h"
#include "bsp_CAN.h"
#include "lvgl.h"
#include "lv_port_disp.h"
#include "ui.h" 
#include "applicationVar.h"

/* USER CODE END Includes */

/* USER CODE BEGIN PD */
#define SPI_FATFS_DEBUG 0
#define LVGL_DEBUG 1

/* USER CODE END PD */

/* USER CODE BEGIN PM */
/*
                   _ooOoo_
                  o8888888o
                  88" . "88
                  (| -_- |)
                  O\  =  /O
               ____/`---'\____
             .'  \\|     |//  `.
            /  \\|||  :  |||//  \
           /  _||||| -:- |||||-  \
           |   | \\\  -  /// |   |
           | \_|  ''\---/''  |   |
           \  .-\__  `-`  ___/-. /
         ___`. .'  /--.--\  `. . __
      ."" '<  `.___\_<|>_/___.'  >'"".
     | | :  `- \`.;`\ _ /`;.`/ - ` : | |
     \  \ `-.   \_ __\ /__ _/   .-` /  /
======`-.____`-.___\_____/___.-`____.-'======
                   `=---='
^^^^^^^^^^^^^^^^^^^^^^^^^^^^^^^^^^^^^^^^^^^^^
            佛祖保佑       永无BUG
*/
/* USER CODE END PM */


/* USER CODE BEGIN PV */
#if SPI_FATFS_DEBUG 
#include "spi.h"
#include "lv_port_fs.h"
#include "ff.h"
uint8_t errorCode,formatSTAT,i;
FATFS fs;//文件系统对象
FIL fp;//文件对象
BYTE work[4096];
extern LV_ATTRIBUTE_MEM_ALIGN uint8_t ui_img_splash_png_data[];
char *write_text="FATFS test success!!!!";
unsigned int write_bytes=0;
char read_buff[8192];
unsigned int read_bytes=0;
#endif
/* USER CODE END PV */

void SystemClock_Config(void);
void MX_FREERTOS_Init(void);
/* USER CODE BEGIN 0 */
#if SPI_FATFS_DEBUG
void SPI_FLASH_WriteTest()
{
	if(!f_open(&fp,"0:test.txt",FA_CREATE_ALWAYS | FA_WRITE))
	{
		printf("open file success!\n");
	}
	else printf("open file failure!\n");
	
	if(!f_write(&fp,(char*)ui_img_splash_png_data,strlen((char*)ui_img_splash_png_data),&write_bytes))
	{
		printf("write success,write_bytes=%d\n",write_bytes);
	}
	else printf("write failure!\n");
 	if(!f_close(&fp))
	{
		printf("close success!\n");
	}
	else printf("close failure!\n");
	if(!f_open(&fp,"0:test.txt",FA_READ))
	{
		printf("open file success!\n");
	}
	else printf("open file failure!\n");
	if(!f_read(&fp,(char*)read_buff,sizeof(read_buff),&read_bytes))
	{
		printf("read success,write_bytes=%d\n",read_bytes);
		printf("test.txt content is :%s\n",read_buff);
	}
	else printf("read failure!\n");
	if(!f_close(&fp))
	{
		printf("close success!\n");
	}
	else printf("close failure!\n");
}
#endif

/* USER CODE END 0 */

/**
  * @brief  The application entry point.
  * @retval int
  */
int main(void)
{
  /* USER CODE BEGIN 1 */
	
//	uint8_t barUpdataFlag = 1;
  /* USER CODE END 1 */
	
  /* MCU Configuration--------------------------------------------------------*/

  /* Reset of all peripherals, Initializes the Flash interface and the Systick. */
  HAL_Init();

  /* USER CODE BEGIN Init */
	//HAL_Delay(200);
  /* USER CODE END Init */

  /* Configure the system clock */
  SystemClock_Config();

  /* Initialize all configured peripherals */
  MX_GPIO_Init();
  MX_DMA_Init();
  MX_FSMC_Init();
  MX_CRC_Init();
  MX_TIM3_Init();
  MX_SPI3_Init();
  MX_USART1_UART_Init(); 
  MX_TIM1_Init();
  MX_USART3_UART_Init();
  MX_TIM4_Init();
  MX_USB_OTG_FS_PCD_Init();
  /* USER CODE BEGIN 2 */
	//   LVGL任务定时器中断
	ws2812_init(12);
	LCD_Init();
	LCD_Clear(BLACK);
	
#if LVGL_DEBUG	
	lv_init();
	lv_port_disp_init();  // lvgl显示接口初始化,放在lv_init()的后面
	//lv_port_fs_init();
	//lv_bmp_init();
	ui_init();
	//HAL_Delay(3000);
	
#endif
#if SPI_FATFS_DEBUG
	formatSTAT = f_mkfs("0:",0,work,sizeof work);
	printf("format stat is :%d\n",formatSTAT);
	errorCode = f_mount(&fs,"0:",1);
	
	if(!errorCode)//挂载外部FLASH)
	{
		printf("mount success!\n");
	}
	else
	{
		printf("Mount Failed!!!errorCode:%d\r\n",errorCode);
	}
	SPI_FLASH_WriteTest();
#endif
  /* USER CODE END 2 */

  /* Init scheduler */
  osKernelInitialize();  /* Call init function for freertos objects (in freertos.c) */
  MX_FREERTOS_Init();

  /* Start scheduler */
  osKernelStart();

  /* We should never get here as control is now taken by the scheduler */
  /* Infinite loop */
  /* USER CODE BEGIN WHILE */
//  while (1)
//  {
//		if(barFlag == 1)
//			sendEventCode();	
//#if LVGL_DEBUG		
//		lv_task_handler(); // lvgl的事务处理	
//#endif
//		HAL_Delay(1);
//		
    /* USER CODE END WHILE */

    /* USER CODE BEGIN 3 */
//  }
  /* USER CODE END 3 */
}

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
/**
  * @brief  Period elapsed callback in non blocking mode
  * @note   This function is called  when TIM2 interrupt took place, inside
  * HAL_TIM_IRQHandler(). It makes a direct call to HAL_IncTick() to increment
  * a global variable "uwTick" used as application time base.
  * @param  htim : TIM handle
  * @retval None
  */
void HAL_TIM_PeriodElapsedCallback(TIM_HandleTypeDef *htim)
{
  if (htim->Instance == TIM2) {
    HAL_IncTick();
  }
  /* USER CODE BEGIN Callback 1 */
	if (htim == (&htim3))
  {	
		lv_tick_inc(1);//lvgl的1ms中断
			//printf("tick\n");
  }
	if(htim == (&htim4))
	{
		msec+=1;
		if(msec == 100)
		{
			msec = 0;
			sec+=1;
		}
		if(sec == 60)
		{
			sec = 0;
			min+=1;
			
		}
		if(min == 60)
		{
			msec = 0;
			min = 0;
			sec = 0;
		}
	}
  /* USER CODE END Callback 1 */
}

/**
  * @brief  This function is executed in case of error occurrence.
  * @retval None
  */
void Error_Handler(void)
{
  /* USER CODE BEGIN Error_Handler_Debug */
  /* User can add his own implementation to report the HAL error return state */
  __disable_irq();
  while (1)
  {
  }
  /* USER CODE END Error_Handler_Debug */
}

#ifdef  USE_FULL_ASSERT
/**
  * @brief  Reports the name of the source file and the source line number
  *         where the assert_param error has occurred.
  * @param  file: pointer to the source file name
  * @param  line: assert_param error line source number
  * @retval None
  */
void assert_failed(uint8_t *file, uint32_t line)
{
  /* USER CODE BEGIN 6 */
  /* User can add his own implementation to report the file name and line number,
     ex: printf("Wrong parameters value: file %s on line %d\r\n", file, line) */
  /* USER CODE END 6 */
}
#endif /* USE_FULL_ASSERT */

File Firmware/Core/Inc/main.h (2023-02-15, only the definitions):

#define LED1_Pin GPIO_PIN_6
#define LED1_GPIO_Port GPIOF
#define LED2_Pin GPIO_PIN_7
#define LED2_GPIO_Port GPIOF
#define BLT_IN_Pin GPIO_PIN_8
#define BLT_IN_GPIO_Port GPIOF
#define BLT_OUT_Pin GPIO_PIN_9
#define BLT_OUT_GPIO_Port GPIOF
#define BLT_RST_Pin GPIO_PIN_10
#define BLT_RST_GPIO_Port GPIOF
#define INPUT1_Pin GPIO_PIN_4
#define INPUT1_GPIO_Port GPIOA
#define INPUT2_Pin GPIO_PIN_5
#define INPUT2_GPIO_Port GPIOA
#define INPUT3_Pin GPIO_PIN_6
#define INPUT3_GPIO_Port GPIOA
#define INPUT4_Pin GPIO_PIN_7
#define INPUT4_GPIO_Port GPIOA
#define INPUT5_Pin GPIO_PIN_4
#define INPUT5_GPIO_Port GPIOC
#define INPUT6_Pin GPIO_PIN_5
#define INPUT6_GPIO_Port GPIOC
#define INPUT8_Pin GPIO_PIN_0
#define INPUT8_GPIO_Port GPIOB
#define INPUT9_Pin GPIO_PIN_1
#define INPUT9_GPIO_Port GPIOB
#define INPUT7_Pin GPIO_PIN_11
#define INPUT7_GPIO_Port GPIOF
#define RST_4G_Pin GPIO_PIN_7
#define RST_4G_GPIO_Port GPIOG
#define PWR_4G_Pin GPIO_PIN_8
#define PWR_4G_GPIO_Port GPIOG
#define INPUTA_Pin GPIO_PIN_10
#define INPUTA_GPIO_Port GPIOG
#define SPI_CS1_Pin GPIO_PIN_6
#define SPI_CS1_GPIO_Port GPIOB
#define canOPEN 0
#define simhubOPEN 1
#define GPIOA_ODR_Addr    (GPIOA_BASE+20) 
#define GPIOB_ODR_Addr    (GPIOB_BASE+20)
#define GPIOC_ODR_Addr    (GPIOC_BASE+20) 
#define GPIOD_ODR_Addr    (GPIOD_BASE+20) 
#define GPIOE_ODR_Addr    (GPIOE_BASE+20)
#define GPIOF_ODR_Addr    (GPIOF_BASE+20)
#define GPIOG_ODR_Addr    (GPIOG_BASE+20) 
#define GPIOH_ODR_Addr    (GPIOH_BASE+20) 
#define GPIOI_ODR_Addr    (GPIOI_BASE+20)
#define GPIOJ_ODR_ADDr    (GPIOJ_BASE+20)
#define GPIOK_ODR_ADDr    (GPIOK_BASE+20) 
#define GPIOA_IDR_Addr    (GPIOA_BASE+16)
#define GPIOB_IDR_Addr    (GPIOB_BASE+16)
#define GPIOC_IDR_Addr    (GPIOC_BASE+16) 
#define GPIOD_IDR_Addr    (GPIOD_BASE+16) 
#define GPIOE_IDR_Addr    (GPIOE_BASE+16) 
#define GPIOF_IDR_Addr    (GPIOF_BASE+16) 
#define GPIOG_IDR_Addr    (GPIOG_BASE+16) 
#define GPIOH_IDR_Addr    (GPIOH_BASE+16) 
#define GPIOI_IDR_Addr    (GPIOI_BASE+16) 
#define GPIOJ_IDR_Addr    (GPIOJ_BASE+16) 
#define GPIOK_IDR_Addr    (GPIOK_BASE+16) 

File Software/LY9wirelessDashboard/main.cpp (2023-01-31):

#include <QGuiApplication>
#include <QQmlApplicationEngine>
#include <QApplication>
#include <QtMqtt/qmqttclient.h>
#include "qmlmqttclient.h"

int main(int argc, char *argv[])
{
    QCoreApplication::setAttribute(Qt::AA_EnableHighDpiScaling);

    QApplication app(argc, argv);

    qmlRegisterType<QmlMqttClient>("MqttClient",1,0,"MqttClient");
    qmlRegisterUncreatableType<QmlMqttSubscription>("MqttClient", 1, 0, "MqttSubscription", QLatin1String("Subscriptions are read-only"));


    QQmlApplicationEngine engine;
    const QUrl url(QStringLiteral("qrc:/main.qml"));
    QObject::connect(&engine, &QQmlApplicationEngine::objectCreated,
                     &app, [url](QObject *obj, const QUrl &objUrl) {
        if (!obj && url == objUrl)
            QCoreApplication::exit(-1);
    }, Qt::QueuedConnection);
    engine.load(url);

    return app.exec();
}

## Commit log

2023-01-15 更新使用CMSISV2版本FreeRTOS,使用事件驱动进程。
2023-01-15 修复计时器BUG.
2023-01-16 BC260Y初始化放入进程，定时器在进入界面后开始启动。
2023-01-16 增加换挡灯条闪烁功能
2023-01-19 添加模拟器显示功能
2023-01-26 更新UI动画，切换屏幕改为淡出效果
2023-01-28 修复CDC接收字符串不完整的问题
2023-01-28 更新界面显示信息，添加刹车踏板开度和油门踏板开度以及圈数显示
2023-01-30 添加simhub配置文件。
2023-01-30 添加控制器驱动，使用USB组合设备.
2023-01-30 添加实车模式和模拟器模式自动识别功能。
2023-01-31 实车与模拟器功能联调
2023-02-04 添加3D模型
    [base.SLDPRT, surface.SLDPRT, 快拆总成.step]
2023-02-06 完成基本结构的建模
    [屏幕罩.stl, 底壳.step, 底板边缘外壳.stl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]
2023-02-08 release the 3D model
    [base.SLDPRT, surface.SLDPRT, 屏幕罩.stl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]
2023-02-08 添加Bom
    [Shifter_Body L.stl, Shifter_Body R.stl, Shifter_Shaft LH.stl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]
2023-02-08 更新Bom
    [Steering_Wheel_BOM.xlsx]
2023-02-09 更新Bom，添加成本预算
    [Steering_Wheel_BOM.xlsx]
2023-02-09 更新装配体
2023-02-14 更新硬件原理图和装配模型。
2023-02-14 update the hardWare
    [Quectel_BC260Y-CN_2D_Dimensions_Revision_History.xlsx, Quectel_BC260Y-CN_2D_Dimensions_V1.0.dwg]
2023-03-11 BC260Y Driver update.
2023-03-23 更新BC260Y驱动保证连接成功率
    [Steering_Wheel_BOM.xlsx]
2023-03-25 更新模拟器模型
2023-03-27 修复界面 10000rpm BUG.
2023-03-27 LVGL 仪表更新
2023-04-06 兼容Motec M800. 修改CAN波特率为1M，添加实车按键控制，待测试。
2023-04-08 Motec Function Bug Fix
    [bsp_CAN.c]
2023-04-11 update M800 Functions. fix the bugs.
    [bsp_CAN.c, main.c]
2023-04-12 更新M800 CAN报文判断条件
2023-04-13 添加ID过滤0X5F0
2023-04-16 FreeRTOS进程内解析CAN报文
2023-04-17 fix the bug of M800
    [bsp_CAN.c]
2023-04-18 车速采集更新
2023-04-21 1.针对油车优化转速灯 2.无线数传CAN报文打包bug修复 3.挡位显示修复 4.界面UI添加低压电池电量显示 5.转速动画圆弧范围优化
    [bsp_BC260Y.c, bsp_WS2812B.c]
2023-04-22 修复换挡灯条死机bug
2023-05-14 更新固件代码架构
2023-05-20 更新3D模型
2023-06-09 1.修正CAN波特率设置 2.SLM模块代码更新 3.3D模型更新
    [Shifter_Body L.stl, Shifter_Body R.stl, Shifter_Shaft LH.stl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]

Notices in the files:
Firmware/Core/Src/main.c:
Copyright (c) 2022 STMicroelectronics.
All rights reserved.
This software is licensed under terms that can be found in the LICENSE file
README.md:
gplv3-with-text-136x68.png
